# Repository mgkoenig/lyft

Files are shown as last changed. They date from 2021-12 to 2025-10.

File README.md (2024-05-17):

# LYFT
LYFT is a sophisticated remote control for the famous IKEA BEKANT desk. It replaces the original controller and adds a number of useful features for more options and convenience. 

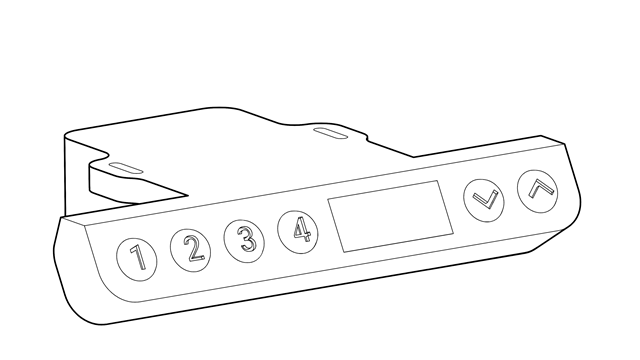
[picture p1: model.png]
lyft_model


Check [tindie](https://www.tindie.com/products/mgkoenig/lyft/) to see a fully assembled version of LYFT in action. 

If you would like to read a featured article about LYFT you can find some on [ikeahackers](https://ikeahackers.net/2024/03/ikea-adjustable-desk.html) or [hackaday](https://hackaday.com/2024/04/18/lyft-standing-up-for-better-ikea-bekant-control/) respectively. 

## Features 
#### Saving Desk Positions  
The controller can store up to four different desk positions. These positions are easily accessable using the four memory buttons.

#### Display 
The controller is equipped with a 3-digit 7-segment display which allows you to read the current desk height either in centimeters or inch. Furthermore, you can adjust the display brigtness as well as the display-on time. If the shown desk height is not accurate you can adjust the value using the 'level correction' feature by plus/minus 9 centimeters. 
  
#### Audio Signals  
In order to give some acoustic feedback the controller has a build-in audio transducer. The volume of the audio signals can be set in the settings menu but also be disabled.
  
#### Automatic Driving Mode
One of the most useful features is the automatic driving mode which allows you to move the desk to a saved position without holding a button all the time. 

#### Safety Pin 
On the basis of the original controller LYFT also supports a safety pin. The pin is needed to move the desk and to unlock the settings menu for changes. It is fully compatible with the original IKEA safety pin which is provided with the BEKANT desk. 

Further details and how to use these features are described in the [manual](/manual.pdf).

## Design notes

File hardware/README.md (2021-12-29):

# LYFT Hardware 
The LYFT hardware consists of two PCB boards. A controller board and an HMI board. 

### Controller Board
The controller board holds the SAM-D21 micrcontroller and handles all the motor control as well as the HMI communication. Desk motors are addressed using the LIN bus while the HMI board is connected via I2C. A buzzer is used to generate sounds and alarms. 

### HMI Board
The HMI board is equipped with an AS1115 display driver to control both the 7-segment display and all six buttons. 

### Library
Parts which are not existent in the standard KiCad library are published here.

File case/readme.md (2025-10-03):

# LyftV9_2 v36 (R1.00.00)

The slicer file was made for the Prusa mk3s+. 

## Print Part Combinations
### Main Body
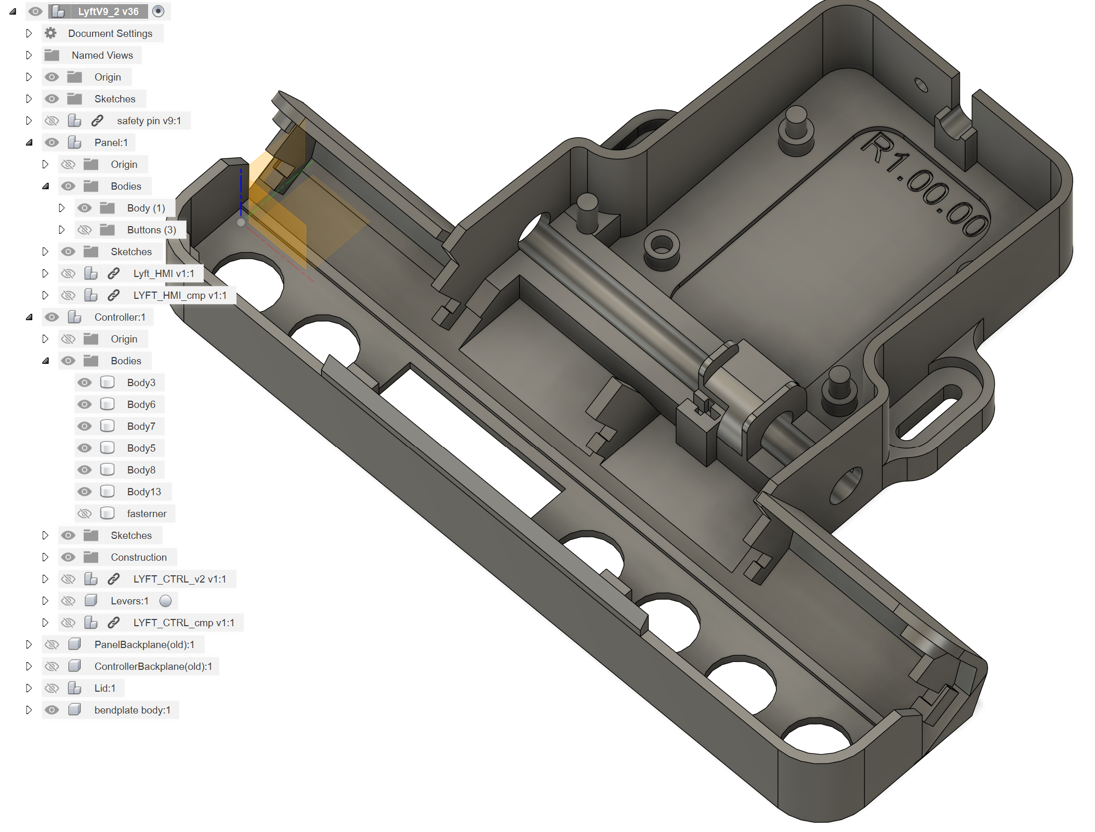
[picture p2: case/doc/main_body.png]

- Component "Panel"
  - Body Group
- Component "Controller"
  - all bodies except "fastener"
  - exclude Component "Levers"
- Component "bendplate body"

### Lid
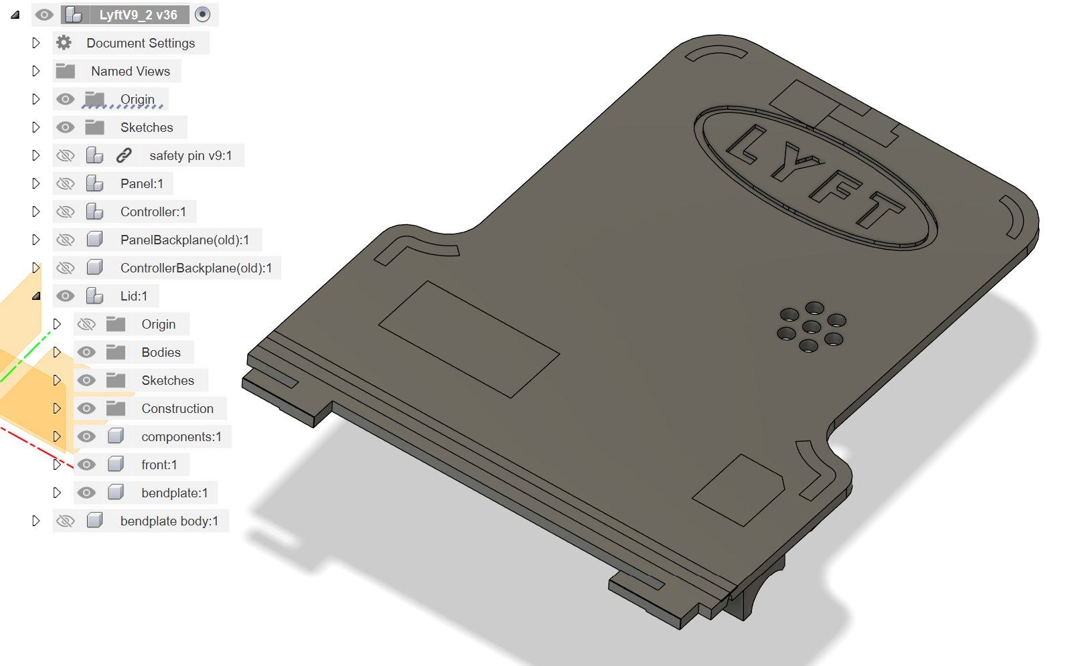
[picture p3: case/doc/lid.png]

- Component "Lid"

### Levers
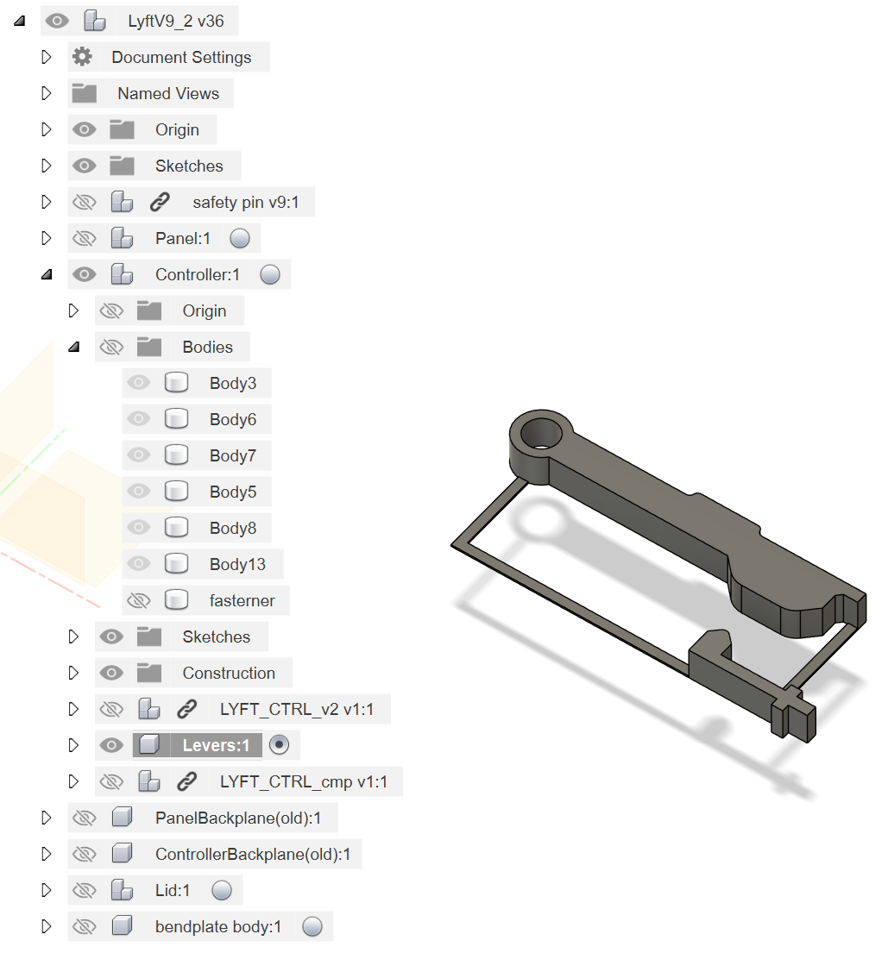
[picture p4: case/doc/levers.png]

- Component "Levers" in "Controller"
  - hide everything else

### Buttons
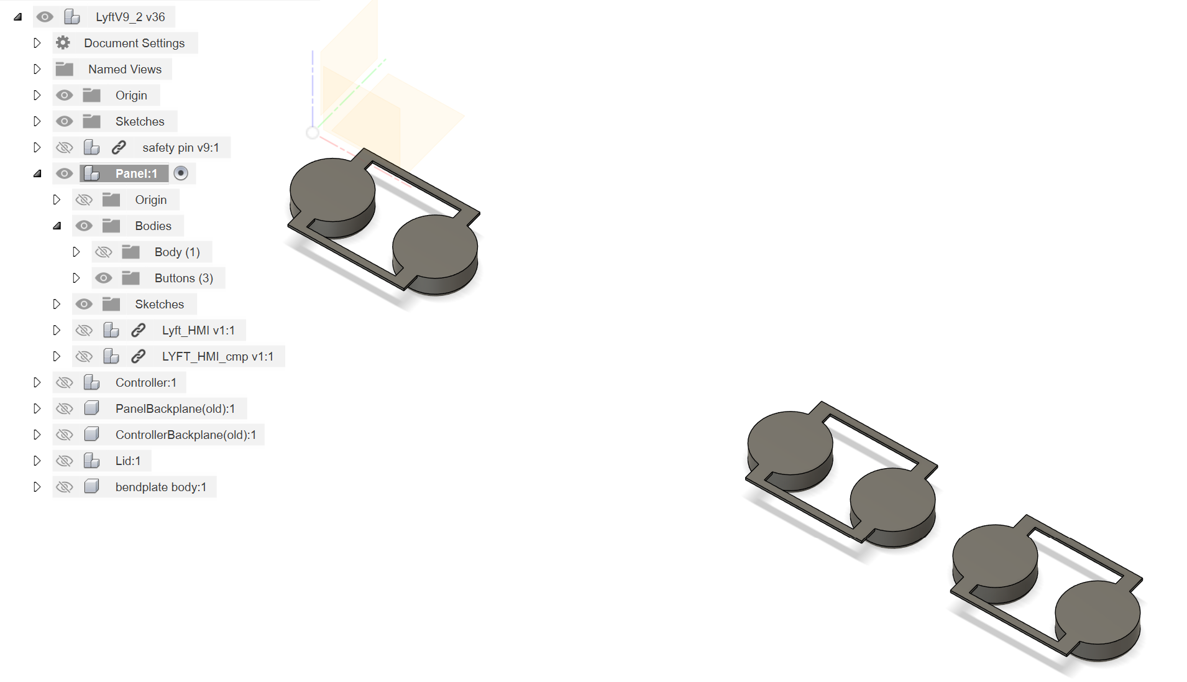
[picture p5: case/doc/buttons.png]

- Body Group "Buttons" in "Panel"
  - hide everything else

### Fasteners
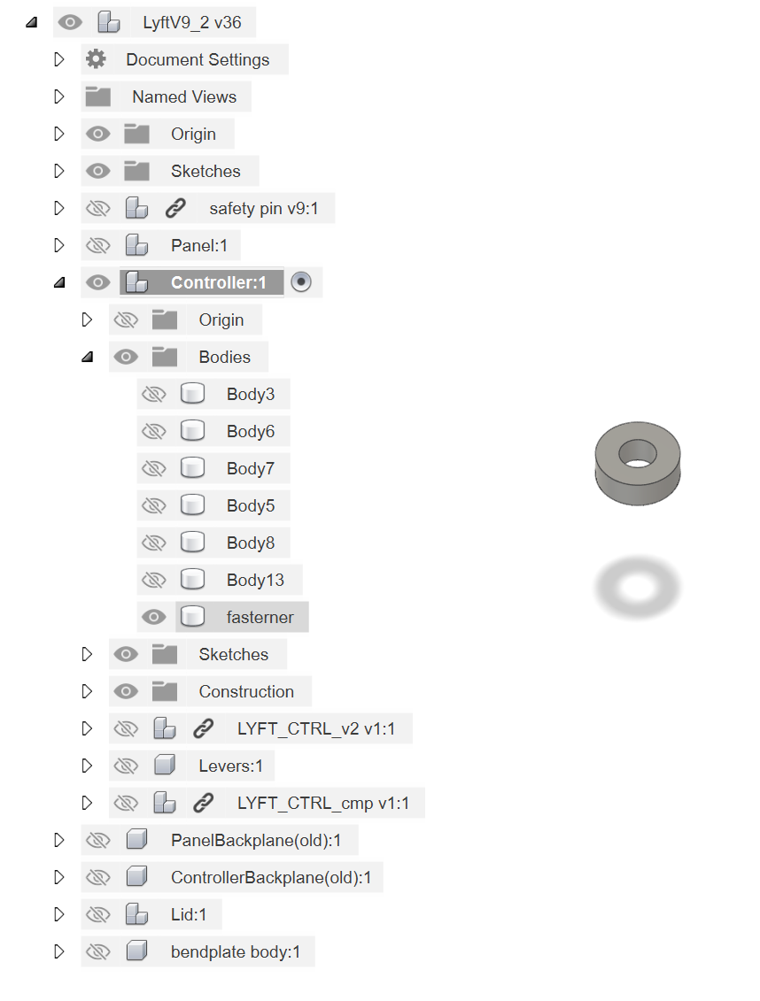
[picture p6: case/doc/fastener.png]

- Body "fastener" in "Controller"
  - hide everything else

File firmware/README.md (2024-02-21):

# LYFT Firmware
The LYFT firmware follows a classical multi-layer approach, consisting of a hardware abstraction layer (HAL), several driver modules and a simple application layer. The driver functions are separated into several files, grouped by their principal tasks. This concept allows you to port the fimrware easily to other platforms. 

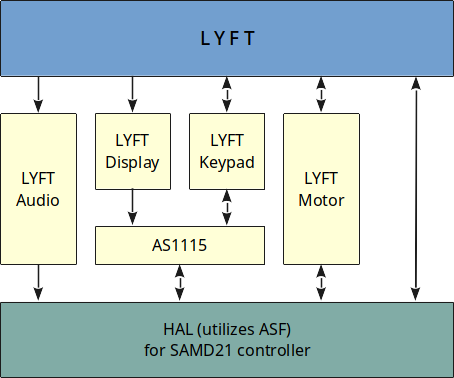
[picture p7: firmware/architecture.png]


The HAL layer utilizes the ASF framework (currently version 3.49.1) for Microchip's SAM MCU's with the following components:
- DAC (callback) [for audio volume control]
- EXTINT (callback) [get notified of keypad inputs]
- NVM [saving configuration and desk positions]
- PORT [GPIO pin control]
- SERCOM I2C (callback) [talk to AS1115 LED controller]
- SERCOM USART (polled) [using a UART module for LIN communication]
- SYSTEM (core system drivers)
- TC (callback) [handling motor timings, keypad timings ond more]
- TCC (callback)

The LYFT drivers are separated into four modules: 
- Audio: all functins related to audio features
- Display: all functions related to the display
- Keypad: all functins to evaluate keystrokes and holding times
- Motor: all functions to control the motors including LIN bus communication

For the AS1115 display driver IC a discrete driver unit was written.

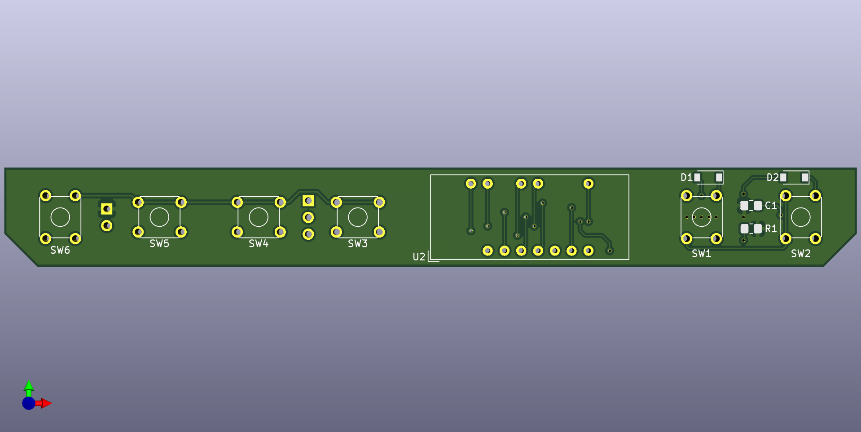
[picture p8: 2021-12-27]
hardware/HMI Board/Rev A/doc/pcb_front.png

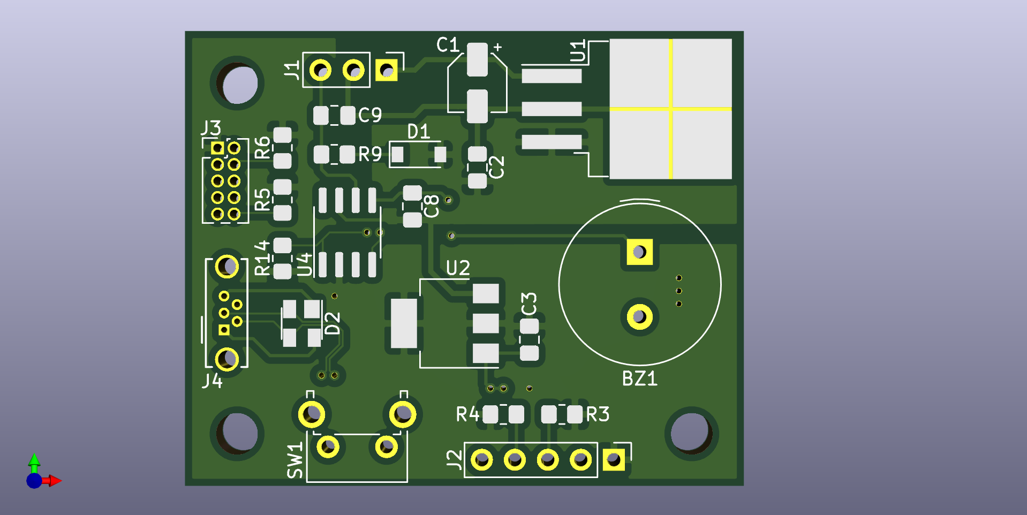
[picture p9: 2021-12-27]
hardware/Controller Board/Rev A/doc/pcb_front.png

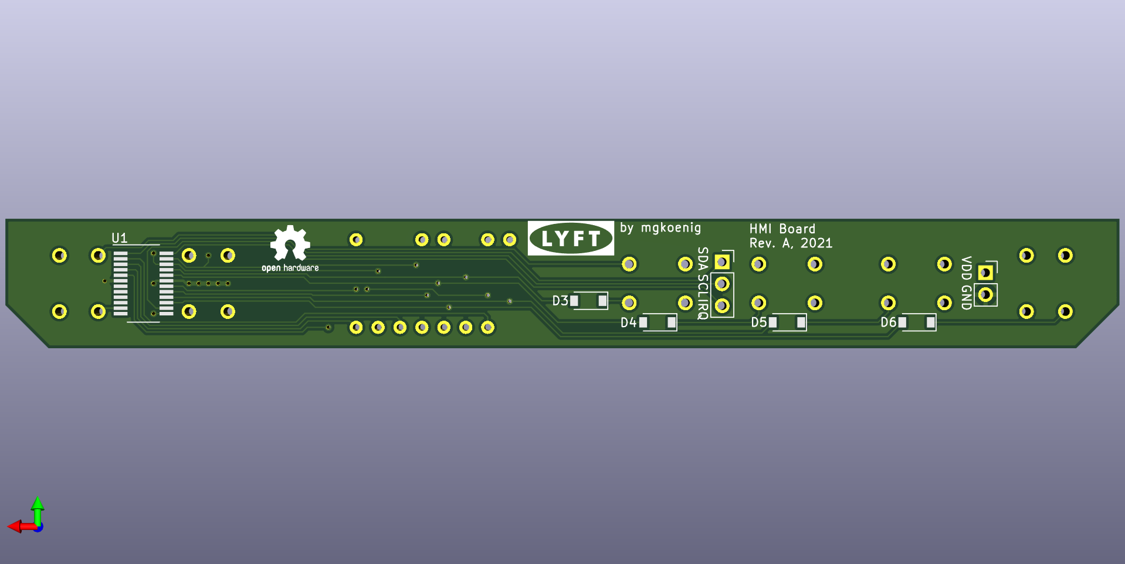
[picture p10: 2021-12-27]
hardware/HMI Board/Rev A/doc/pcb_back.png

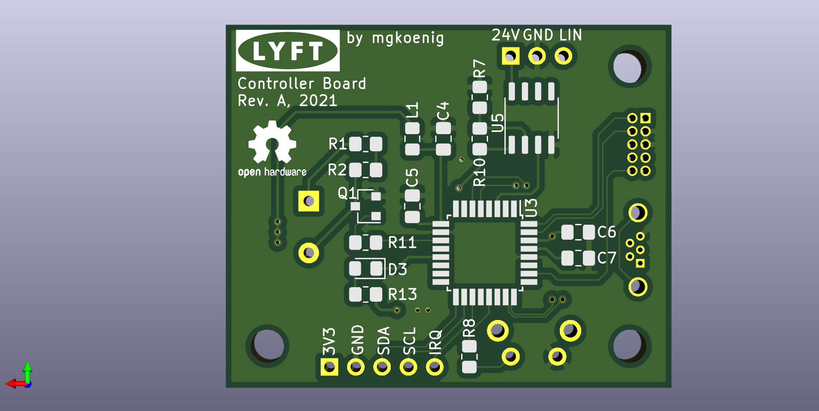
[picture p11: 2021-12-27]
hardware/Controller Board/Rev A/doc/pcb_back.png

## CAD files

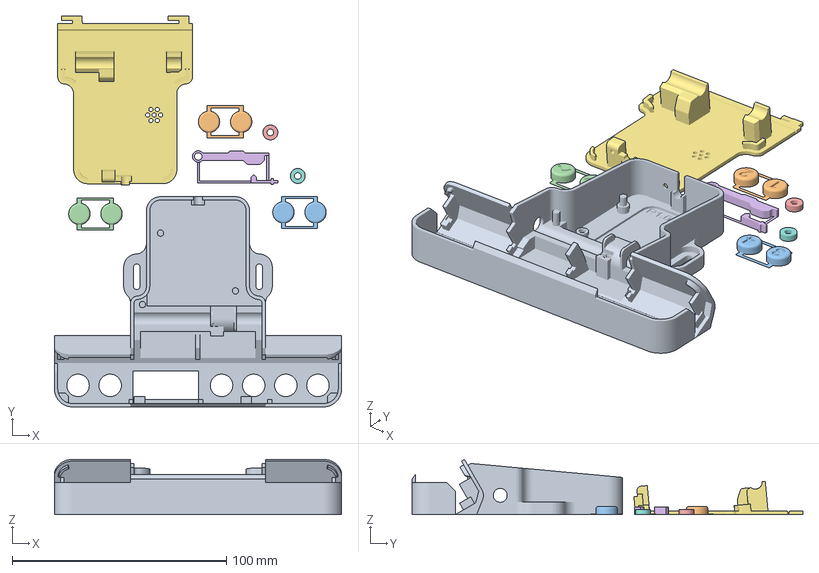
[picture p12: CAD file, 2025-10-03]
case/Lyft_caseR1.3mf
134.2 x 182.5 x 25.8 mm
LyftV9_2 v35 controller R1.00.00.stl
LyftV9_2 v35 buttons_12.stl
LyftV9_2 v35 buttons_34.stl
LyftV9_2 v35 buttons_ud.stl
LyftV9_2 v35 fastener.stl x 2
LyftV9_2 v35 levers.stl
LyftV9_2 v35 Lid R1.00.00.stl

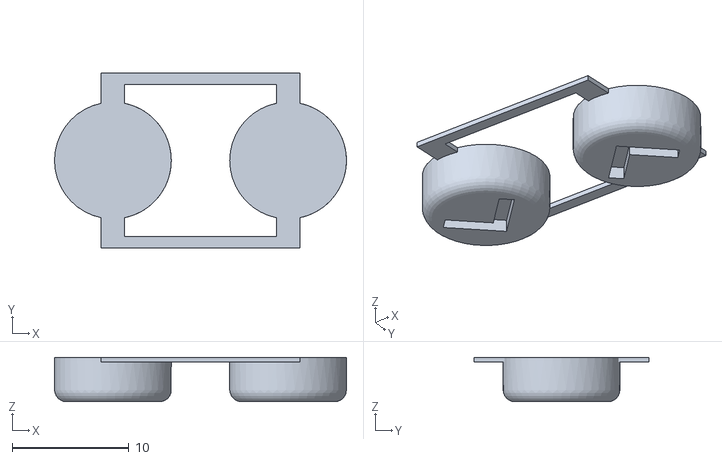
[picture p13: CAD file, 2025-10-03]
case/Lyft_caseR1_buttons_ud.stl
25.0 x 15.0 x 3.80

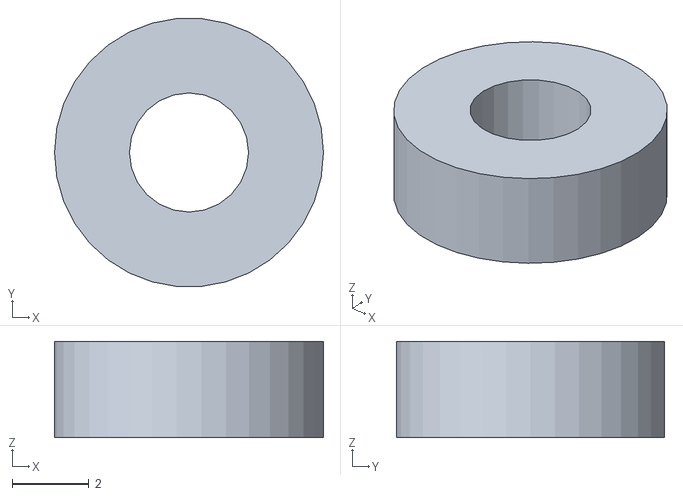
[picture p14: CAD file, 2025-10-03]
case/Lyft_caseR1_fastener.stl
7.00 x 6.97 x 2.50

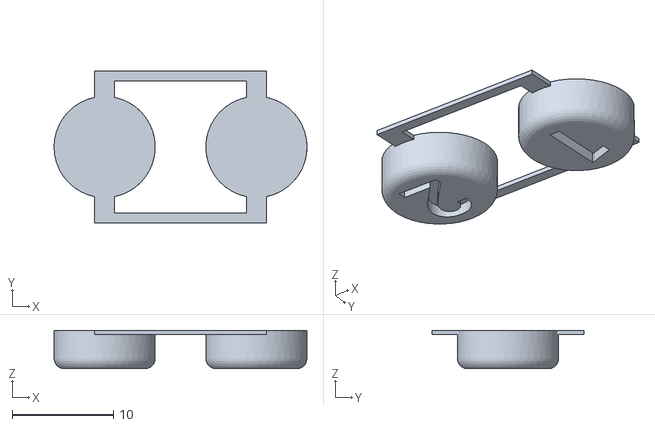
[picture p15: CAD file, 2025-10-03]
case/Lyft_caseR1_buttons_12.stl
25.0 x 15.0 x 3.80

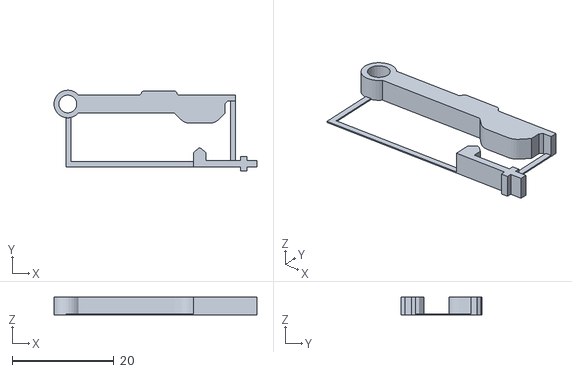
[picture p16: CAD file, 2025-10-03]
case/Lyft_caseR1_levers.stl
39.9 x 15.8 x 3.50

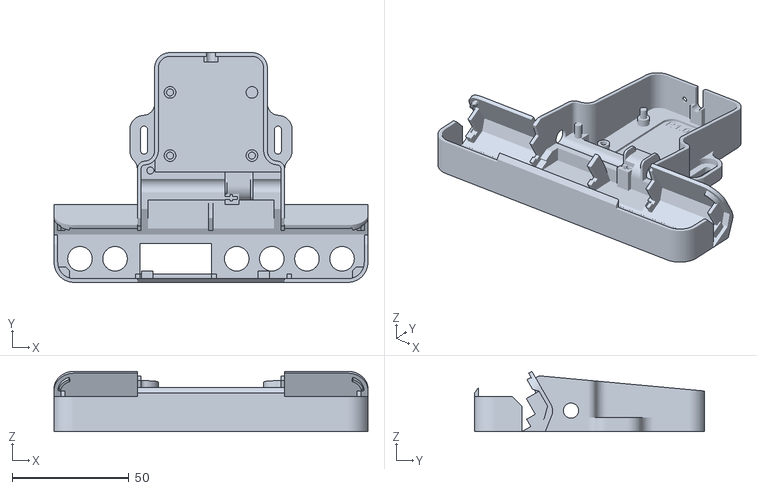
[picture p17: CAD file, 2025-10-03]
case/Lyft_caseR1_controller.stl
134.2 x 98.2 x 25.8

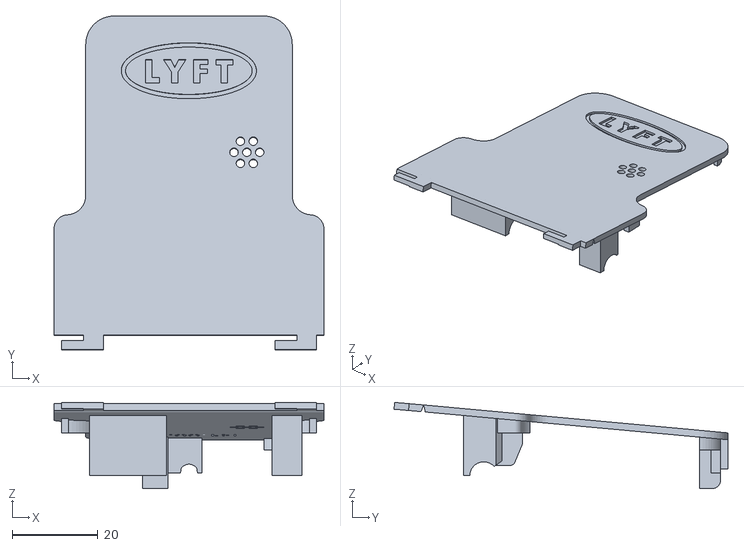
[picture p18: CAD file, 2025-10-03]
case/Lyft_caseR1_lid.stl
63.0 x 77.9 x 20.1

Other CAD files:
case/Lyft_caseR1_buttons_34.stl

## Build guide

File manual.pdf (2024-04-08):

# LYFT


### I M P O R TA N T I N F O R M AT I O N

LYFT is a sophisticated remote control for electric height adjustable desks, compatible with

the famous IKEA BEKANT desk. Designed as a plug & play solution, you can easily replace

your originally provided remote control. LYFT comes completely assembled and is ready to

use out of the box.

This project is an open-source DIY project and comes therefore without any liability or

warranty. Usage of LYFT is always at your own risk. The originator is not liable of any

damage | the | remote | might | cause. | All | source | files | are | published | on | GitHub

(github.com/mgkoenig/lyft) and licenced under the GPL-3.0 license. Feel free to take a closer

look at the design or to improve LYFT with even more useful features customized to your

needs.

All product and company names are trademarks™ or registered® trademarks of their

respective holders. Use of them does not imply any affiliation with or endorsement by

them. IKEA is a registered trademark of Inter IKEA Systems BV.

Disclaimer of liability: In no event shall the originator be liable for any direct, indirect,

punitive, incidental, special, consequential damages, to property or life, whatsoever

arising out of or connected with the use or misuse of this product.

Exclusions from warranties: By purchasing this product you expressly agree that use of this

product is at your sole risk. The originator does not and cannot warrant that the product

will operate without errors.

All information and products described in this manual are provided on an “AS IS” basis.

The originator does not make any representations or warranties of any kind, express or

implied as to the operation of this product or the information made available to you,

including implied warranties of merchantability and fitness for a particular purpose.

Furthermore, the originator's warranties for this product exclude any claims by the

customer based on defects in the product caused by the customer, or by third parties

beyond the originator's control.

2 | Document version 1.0 (02/2024)

### F U N C T I O N A L L AY O U T

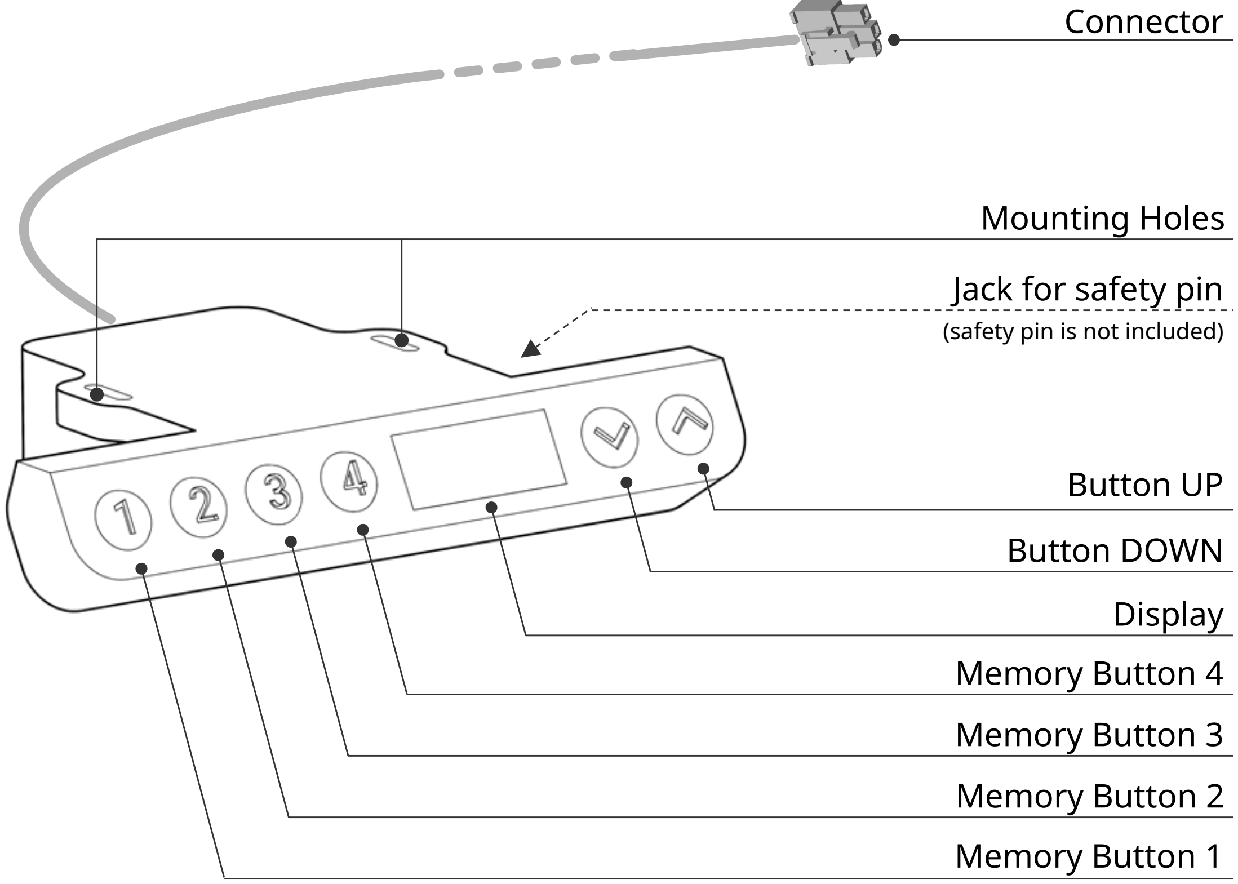
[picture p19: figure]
Connector; Button UP; Button DOWN; Display; Memory Button 4; Memory Button 3; Memory Button 2; Memory Button 1; Jack for safety pin; Mounting Holes; (safety pin is not included)

### I N S TA L L AT I O N

In order to use LYFT, choose your preferred handling side and mount the remote control

on the bottom edge of the desk. Use the destined mounting holes on the housing. Since

no screws are provided with the shipment, you might use the original screws which were

delivered together with the desk or use any two conventional [3 x 16mm] or [4 x 5/8”]

wood screws instead.

Finally plug the cable into its designated connector on the motor box. You can find the

motor box on top of each leg (beneath the table top). If you’re uncertain how to connect

the cable, refer to the original IKEA BEKANT assembly instructions.

Compatible with firmware version 1.1.0. | 3

### B A S I C F E AT U R E S

S A F E T Y P I N

LYFT is equipped with a safety mechanism to prevent unintended desk movements.

Therefore, a safety pin must be plugged in whenever you want to change the desk height

or configuration settings. The safety pin is not provided with the LYFT remote control, but

fully compatible with the safety pin that comes with your IKEA BEKANT desk. If you have

lost your pin, you can easily (and mostly for free) order it as a spare part from your local

IKEA store. Please find the correct part number in the original assembly instructions. If no

safety pin is connected, all features are locked and the display shows the following screen:

M O V I N G U P

To move your desk upwards, just press and hold the UP button on your LYFT remote

control. The motors will automatically stop as soon as you release the button or the upper

limit of the height is reached.

M O V I N G D O W N

To move your desk downwards, just press and hold the DOWN button on your LYFT

remote control. The motors will automatically stop as soon as you release the button or

the lower limit of the height is reached.

M O V I N G T O A S A V E D P O S I T I O N

If you have previously saved a comfortable desk position to one of the memory buttons

(see the description in the upcoming settings chapter), you can move the desk to this

height by pressing and holding the corresponding button. In case no position was saved

so far, the display shows the following screen:

### S E T T I N G S M E N U

E N T E R T H E S E T T I N G S M E N U

In order to make any changes of the settings or to save a current desk position, you need

to enter the settings menu. The menu is accessed by pressing the UP and DOWN buttons

simultaneously for at least 2 seconds.

N A V I G A T E T H E S E T T I N G S M E N U

You can walk through the settings menu by using the UP and DOWN buttons to scroll to

the next or previous page respectively.

L E A V E T H E S E T T I N G S M E N U

To exit the settings menu nothing special has to be done. Six seconds after the last button

was pressed, the menu will save all its current settings and return to its default screen,

showing the desk height.

Compatible with firmware version 1.1.0. | 5

2 sec.

S A V E A P O S I T I O N [ P ]

To save the current desk position, just enter the settings menu. The first entry of the menu

shows a [P] which stands for position. By pushing one of the four memory buttons you will

save the current height to the selected button.

D I S P L A Y B R I G H T N E S S [ L ]

You can change the brightness of the display to four different levels. Navigate within the

settings menu to page [L]. Then, select the intensity by pushing one of the four memory

buttons. Each button sets the brightness to a pre-defined value.

A U D I O C O N T R O L [ A ]

LYFT is equipped with a built-in audio transducer to generate audio signals and alarms.

You can set the volume of these signals or turn them off completely. Navigate to menu

page [A] and set your preferred loudness pushing one of the four memory buttons. Button

1 will turn this feature off while the others set a certain volume level. A beep tone will

demonstarte the selected volume after each keystroke.

D I S P L A Y - O N T I M E [ F ]

After pushing a button or adjusting the desk height to your preferred position, the display

will stay on for a couple of seconds. You can change the display-on time on menu page [F].

Choose between 5, 10, 15 or 20 seconds display-on time using the memory buttons.

M E A S U R E M E N T U N I T [ U ]

By default the height of the desk is shown in centimeters. However, you can change the

dispayed unit to inch. Go to the unit page [U] within the menu and select your preferred

measurement unit using memory button 1 or 2.

D E S K M O V I N G M O D E [ G ]

LYFT supports two driving modes to move the desk to saved position – either manually

(‘hand-driven’) or automatically. When Hand-driven mode is selected, you need to press

and hold the designated memory button until its final desk height is reached. If Automatic

mode is selected, you just need to press the memory button for 1.5 seconds, then the

desk moves by itself to the final position without further interaction. An automatically

moving desk can be stopped by pushing any button on the remote control. Use memory

buttons 1 or 2 to select your preffered moving mode.

Please note: manual mode is safer while automatic mode is more comfartable.

L E V E L C O R R E C T I O N [ C ]

The shown desk height might not be accurate due to level adjustment screws or a thicker

tabletop. Therefore, you have the opportunity to tune the displayed position. Go to the

level correction page [C] and set an offset value to the current height. The offset range is

between plus/minus 9 centimeters. The offset value is always set as centimeter value – no

matter which measurement unit you have selected. Use memory buttons 1 or 2 to

increase or decrease the value.

Compatible with firmware version 1.1.0. | 7

D R I F T I N F O R M A T I O N [ d ]

This menu page is just an informational entry. The drift value tells you the absolute

variation of both motor positions to each other (the smaller the value the better). However,

please keep in mind, this value does not represent centimeters or inches – it’s related to

an internal counting value.

### T R O U B L E S H O O T I N G

In rare cases, it might happen that the motors don’t respond to entries of the LYFT remote.

This error is related to a failed initialization process during the start up phase, when the

remote was connected to the motor box.

In such a case, please disconnect your IKEA BEKANT desk from the power outlet for five

minutes and try again. You can still double-check the flawless operation of your desk using

the original remote control.

### A C K N O W L E D G M E N T S

Many thanks to Marian for his generosity and support! He enriched this project

continuously with great ideas, designed and produced a fabulous housing for the LYFT

remote control.

Thanks to Greg Cormier and his megadesk project (github.com/gcormier/megadesk) for

sharing his findings about the IKEA BEKANT functionality and bus communication.

All icons by icons8.com.

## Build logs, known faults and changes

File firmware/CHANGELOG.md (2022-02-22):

# Changelog

## Version 1.0.0 (22 Feb 2021)
Initial commit. This version runs stable on the provided hardware (both boards Rev A) and includes the following features and drivers: 
- Desk moving up/down
- Four memory positions
- Display shows current desk height as cm or inch value (unit control)
- Display brightness control
- Audio feedback (with volume control)
- Level correction (to adjust the shown desk height)
- Tells the drift of both motors
- Support of the safety pin

User settings (like display brightness, volume control, desk positions) can be stored permanently to the NVM.

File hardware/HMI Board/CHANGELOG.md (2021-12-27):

# Changelog
All notable changes to this project will be documented in this file.
## Revision A (Dec. 2021)
### Features:
- 130x15mm board size
- AS1115 display driver to control 7-segment display and read button states
- 3-digit 7-segment display
- 6 tactile switches

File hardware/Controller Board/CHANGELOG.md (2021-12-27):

# Changelog

All notable changes to this project will be documented in this file.

## Rev. A (Dec. 2021)
### Features
- 43x35mm board size
- SAM-D21 controller
- Buzzer for audio signals
- USB interface placed but unused

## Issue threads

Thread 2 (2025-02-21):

Add case design

black9404, 2025-02-21:
Could you please add the STL files for the case? Would be nice to be able 3D print it to make changes and possible improvements

mgkoenig, 2025-10-03:
Sorry for the delay. The STL files of the case are now available.

Closed 2025-10-03.

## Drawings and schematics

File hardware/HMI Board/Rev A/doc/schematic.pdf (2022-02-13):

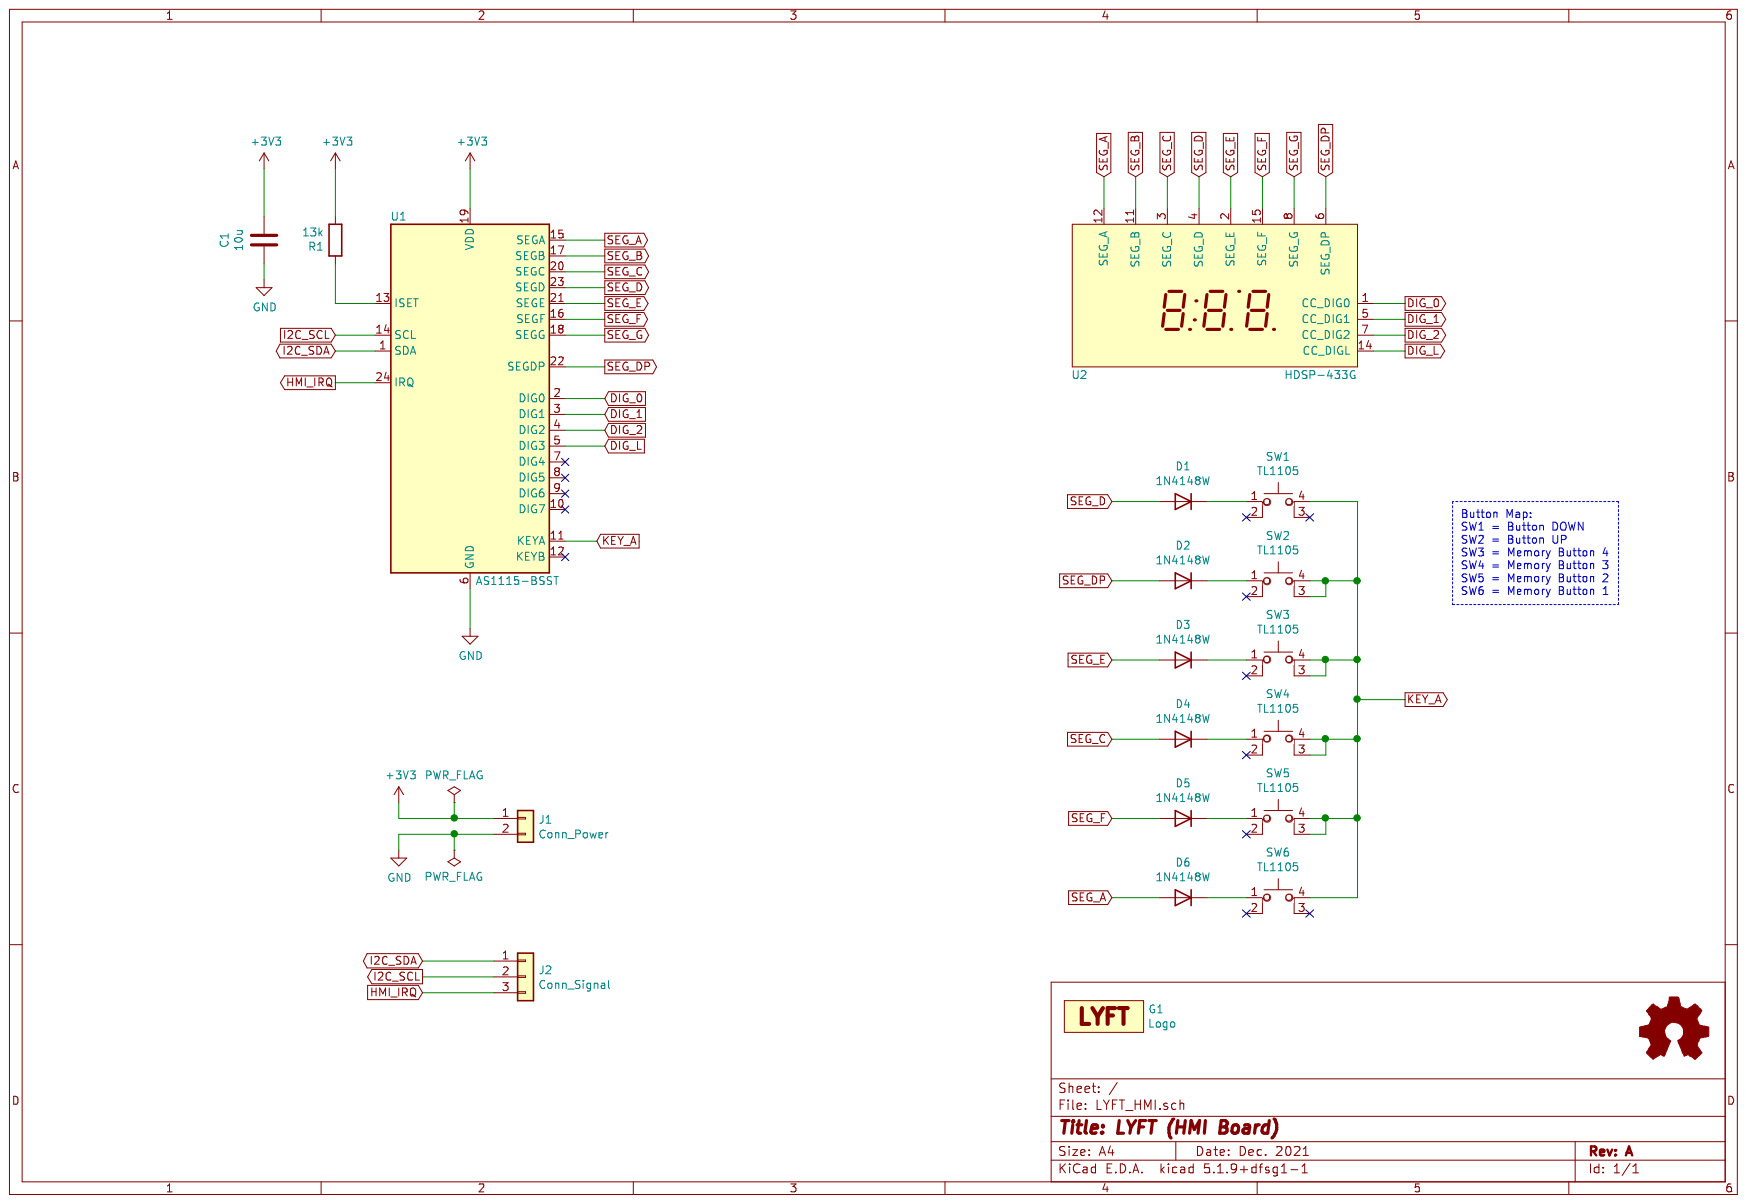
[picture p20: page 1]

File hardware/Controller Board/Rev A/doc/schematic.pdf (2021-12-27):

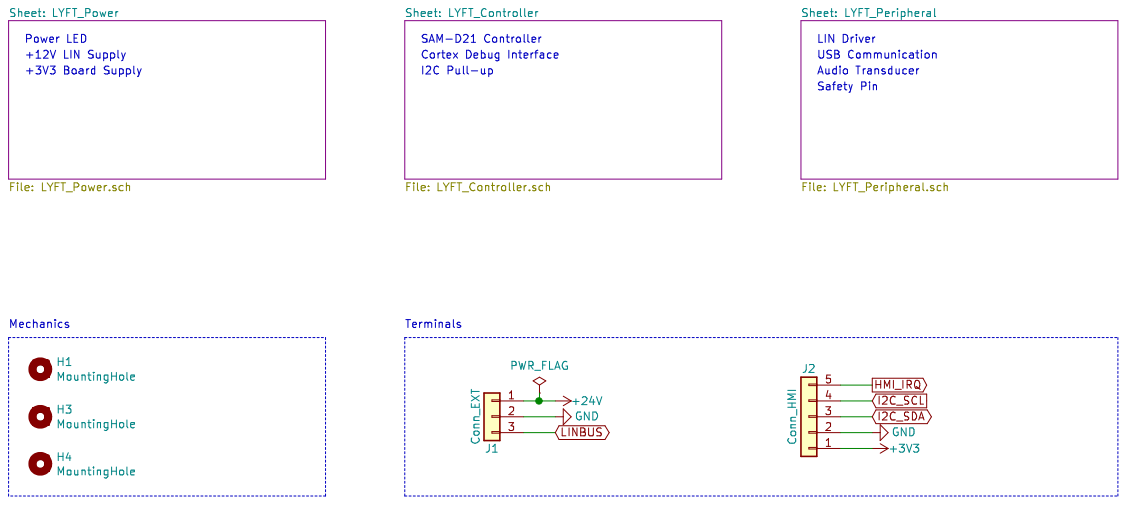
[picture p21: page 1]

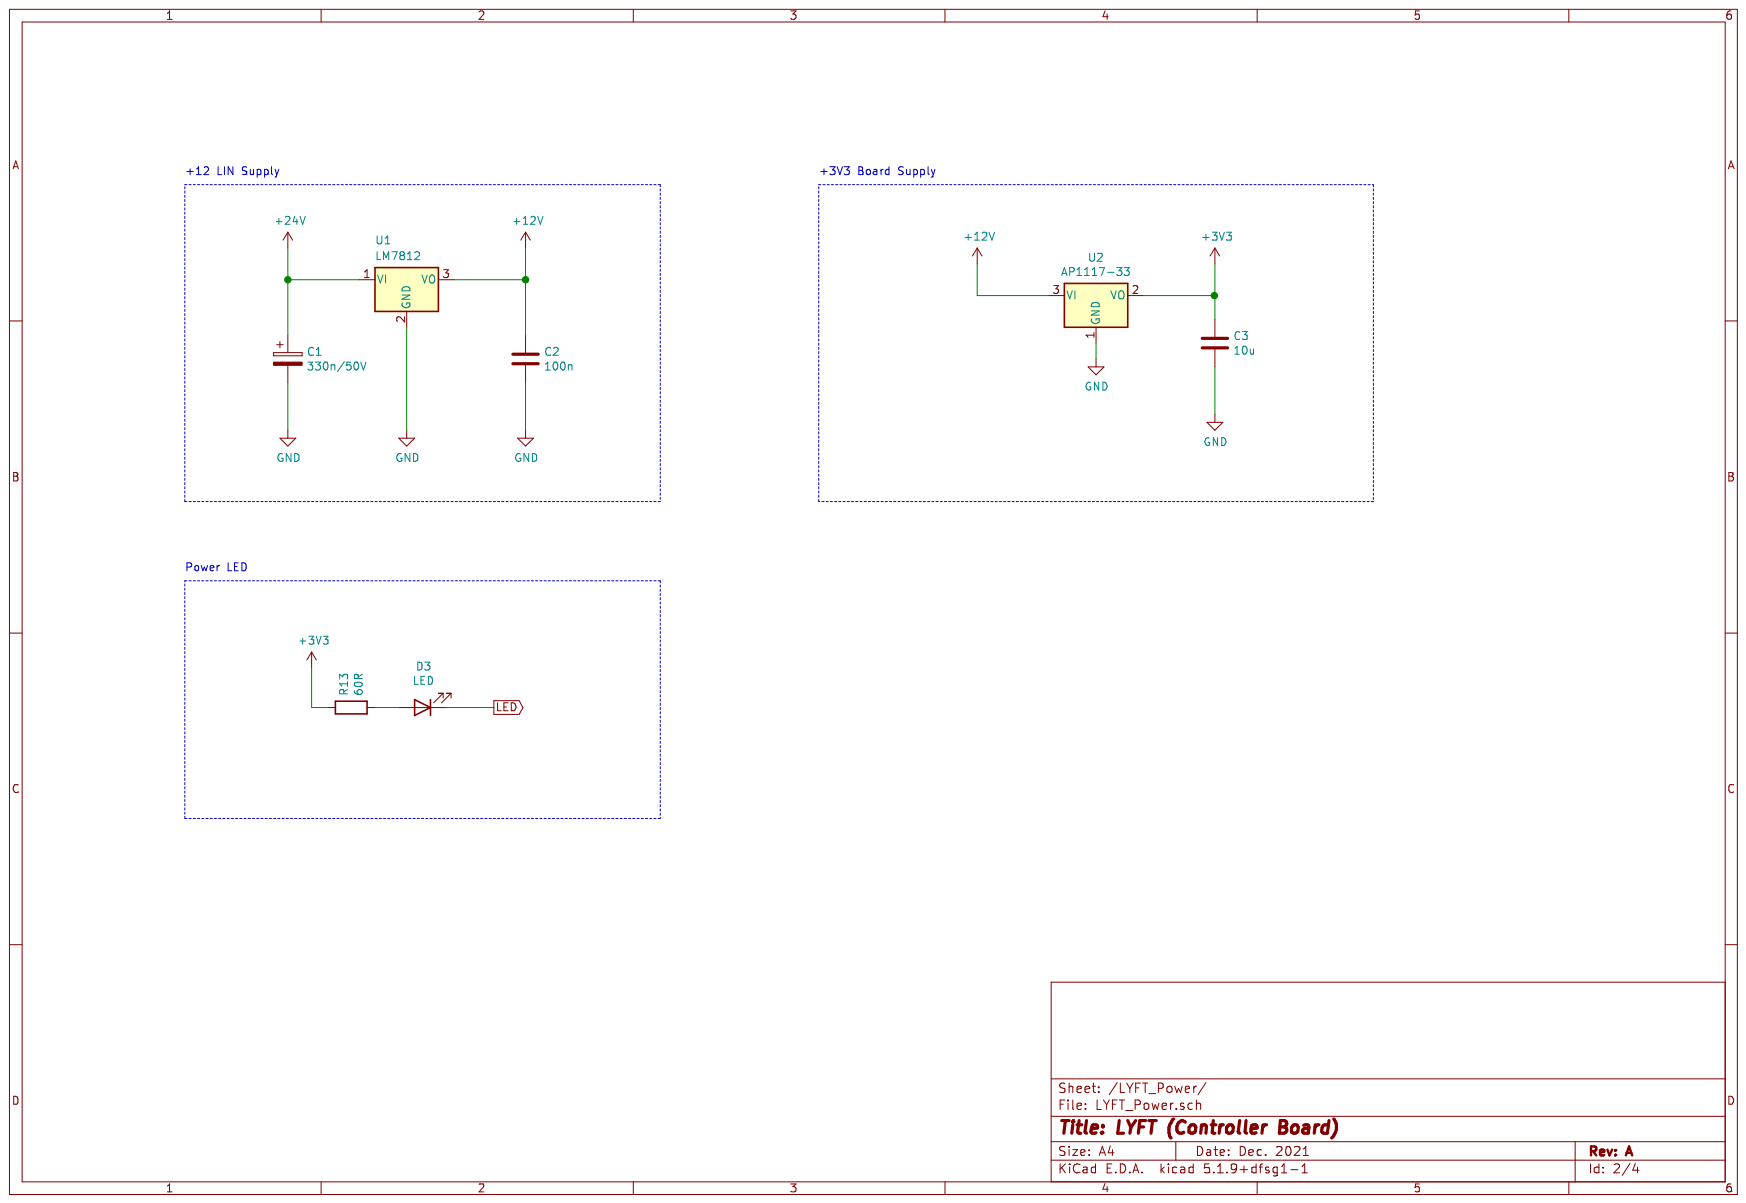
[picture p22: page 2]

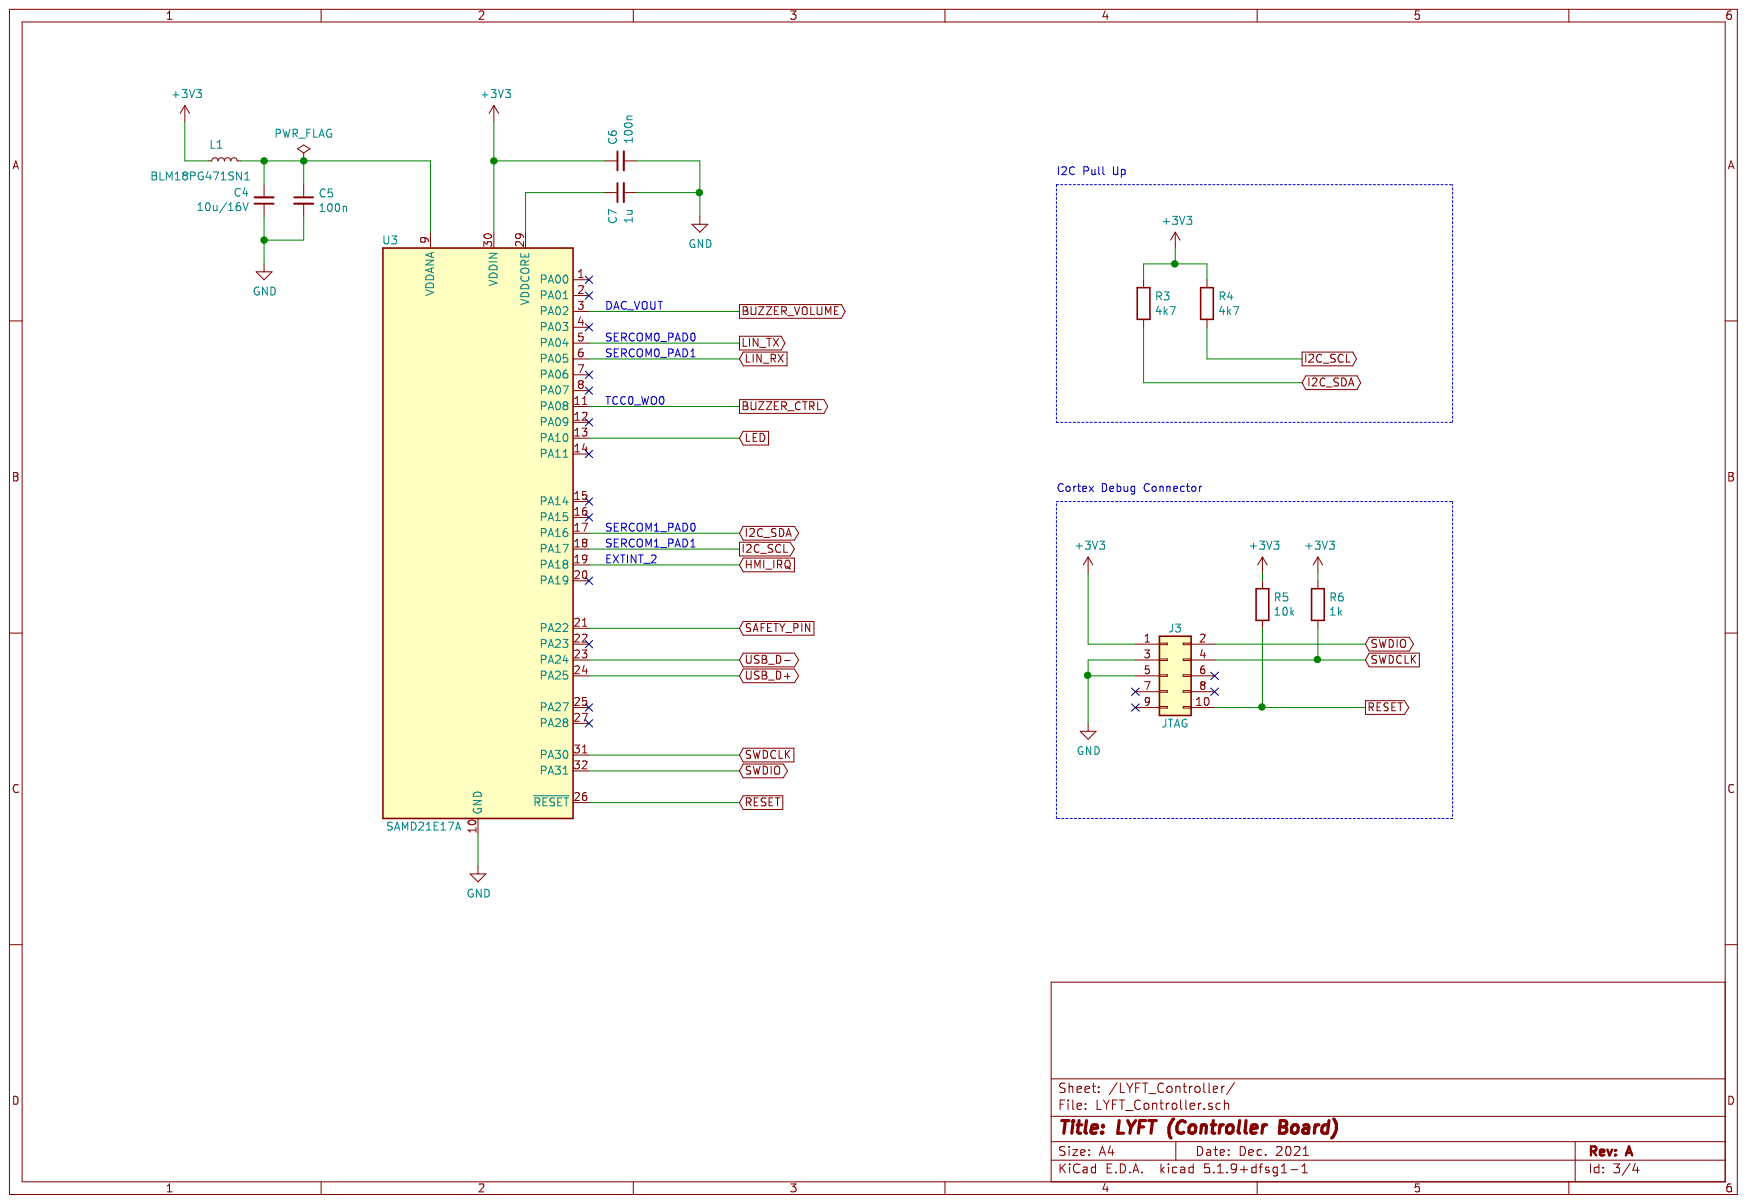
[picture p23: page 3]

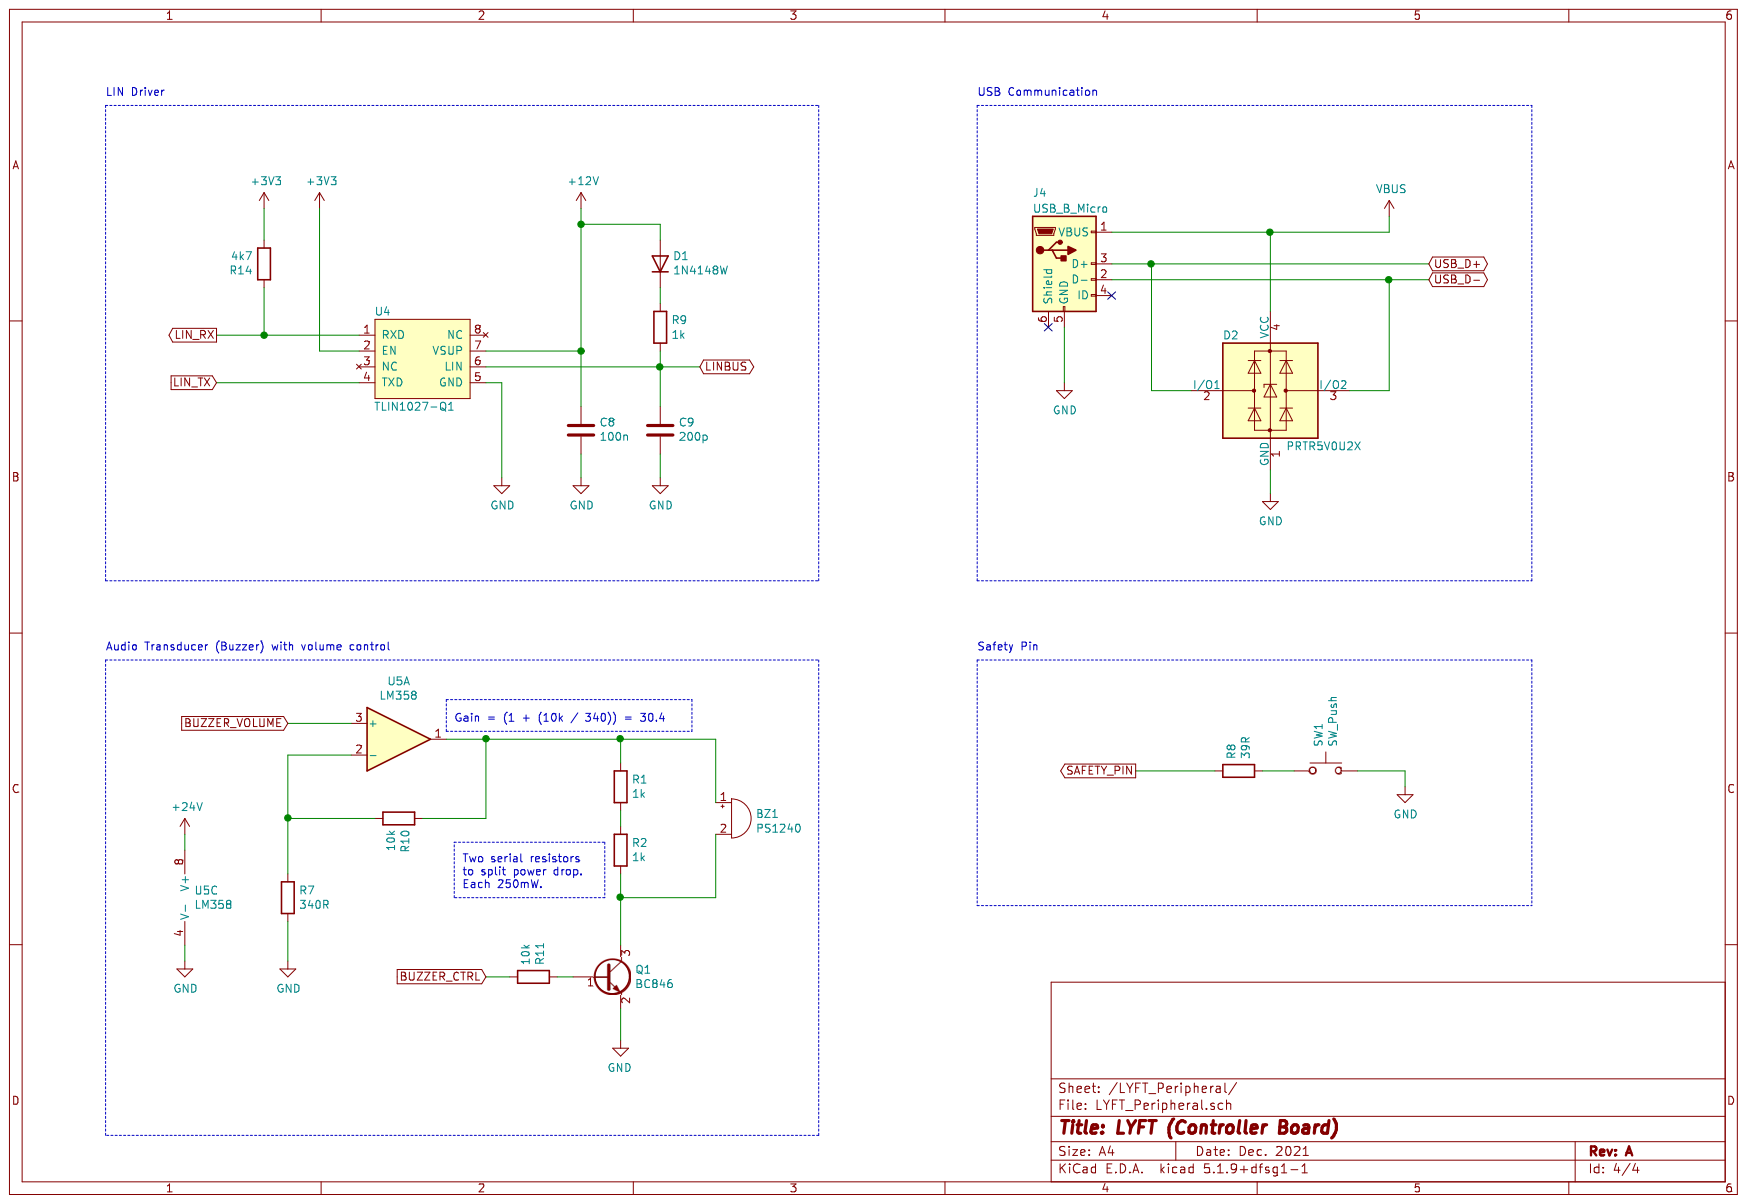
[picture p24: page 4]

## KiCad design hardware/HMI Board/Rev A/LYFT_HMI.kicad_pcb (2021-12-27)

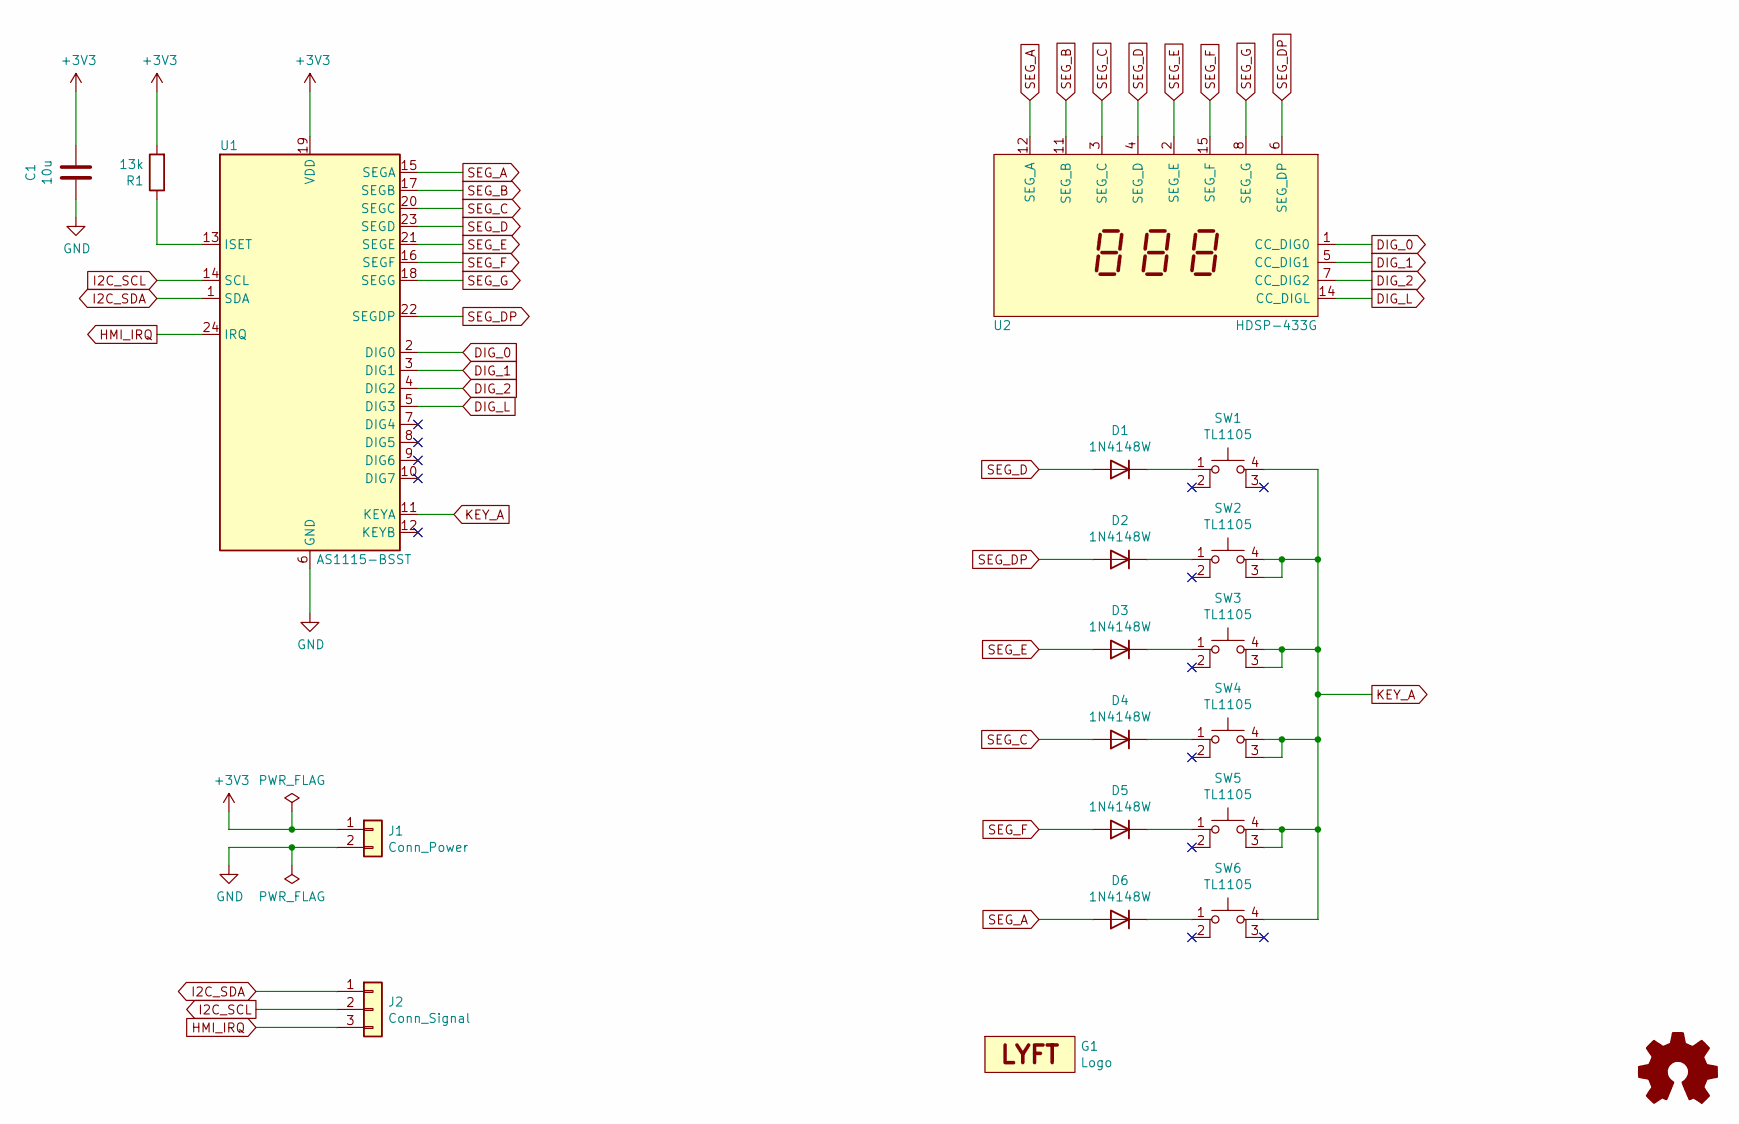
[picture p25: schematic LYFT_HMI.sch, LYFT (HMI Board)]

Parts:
C1: 10u; C_0805_2012Metric_Pad1.18x1.45mm_HandSolder
D1, D2, D3, D4, D5, D6: 1N4148W; D_SOD-123
G1: Logo; LYFT-Logo_10x4
J1: Conn_Power; PinSocket_1x02_P2.54mm_Vertical
J2: Conn_Signal; PinSocket_1x03_P2.54mm_Vertical
R1: 13k; R_0805_2012Metric_Pad1.20x1.40mm_HandSolder
SW1, SW2, SW3, SW4, SW5, SW6: TL1105; SW_TH_Tactile_Omron_B3F-10xx_Center
U1: AS1115-BSST; QSOP-24_3.9x8.7mm_P0.635mm
U2: HDSP-433G; HDSP-433

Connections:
+3V3: C1.1, J1.1, R1.2, U1.19 (VDD)
DIG_0: U1.2 (DIG0), U2.1 (CC_DIG0)
DIG_1: U1.3 (DIG1), U2.5 (CC_DIG1)
DIG_2: U1.4 (DIG2), U2.7 (CC_DIG2)
DIG_L: U1.5 (DIG3), U2.14 (CC_DIGL)
GND: C1.2, J1.2, U1.6 (GND)
HMI_IRQ: J2.3, U1.24 (IRQ)
I2C_SCL: J2.2, U1.14 (SCL)
I2C_SDA: J2.1, U1.1 (SDA)
KEY_A: SW1.4 (A), SW2.3 (K), SW2.4 (A), SW3.3 (K), SW3.4 (A), SW4.3 (K), SW4.4 (A), SW5.3 (K), SW5.4 (A), SW6.4 (A), U1.11 (KEYA)
unnamed: D1.1 (K), SW1.1
unnamed: D2.1 (K), SW2.1
unnamed: D3.1 (K), SW3.1
unnamed: D4.1 (K), SW4.1
unnamed: D5.1 (K), SW5.1
unnamed: D6.1 (K), SW6.1
unnamed: R1.1, U1.13 (ISET)
SEG_A: D6.2 (A), U1.15 (SEGA), U2.12 (SEG_A)
SEG_B: U1.17 (SEGB), U2.11 (SEG_B)
SEG_C: D4.2 (A), U1.20 (SEGC), U2.3 (SEG_C)
SEG_D: D1.2 (A), U1.23 (SEGD), U2.4 (SEG_D)
SEG_DP: D2.2 (A), U1.22 (SEGDP), U2.6 (SEG_DP)
SEG_E: D3.2 (A), U1.21 (SEGE), U2.2 (SEG_E)
SEG_F: D5.2 (A), U1.16 (SEGF), U2.15 (SEG_F)
SEG_G: U1.18 (SEGG), U2.8 (SEG_G)

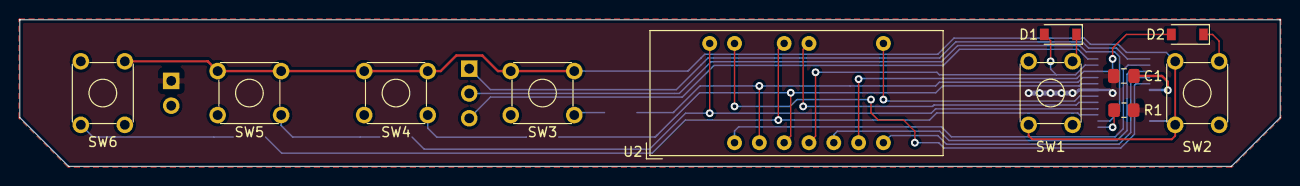
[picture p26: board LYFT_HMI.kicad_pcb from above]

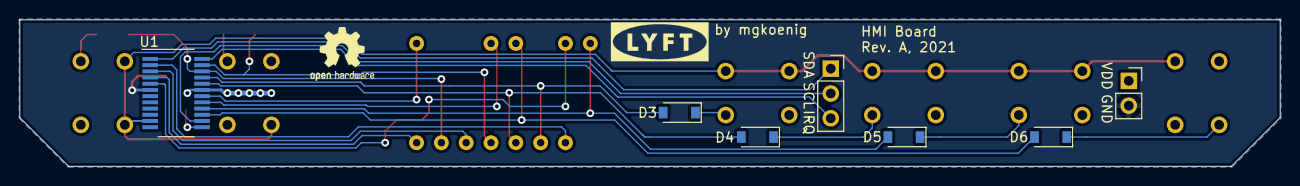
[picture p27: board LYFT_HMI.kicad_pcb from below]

Board: 2 copper layers, 129.0 x 15.0 mm, 19 parts (8 on the bottom side), 25 nets.

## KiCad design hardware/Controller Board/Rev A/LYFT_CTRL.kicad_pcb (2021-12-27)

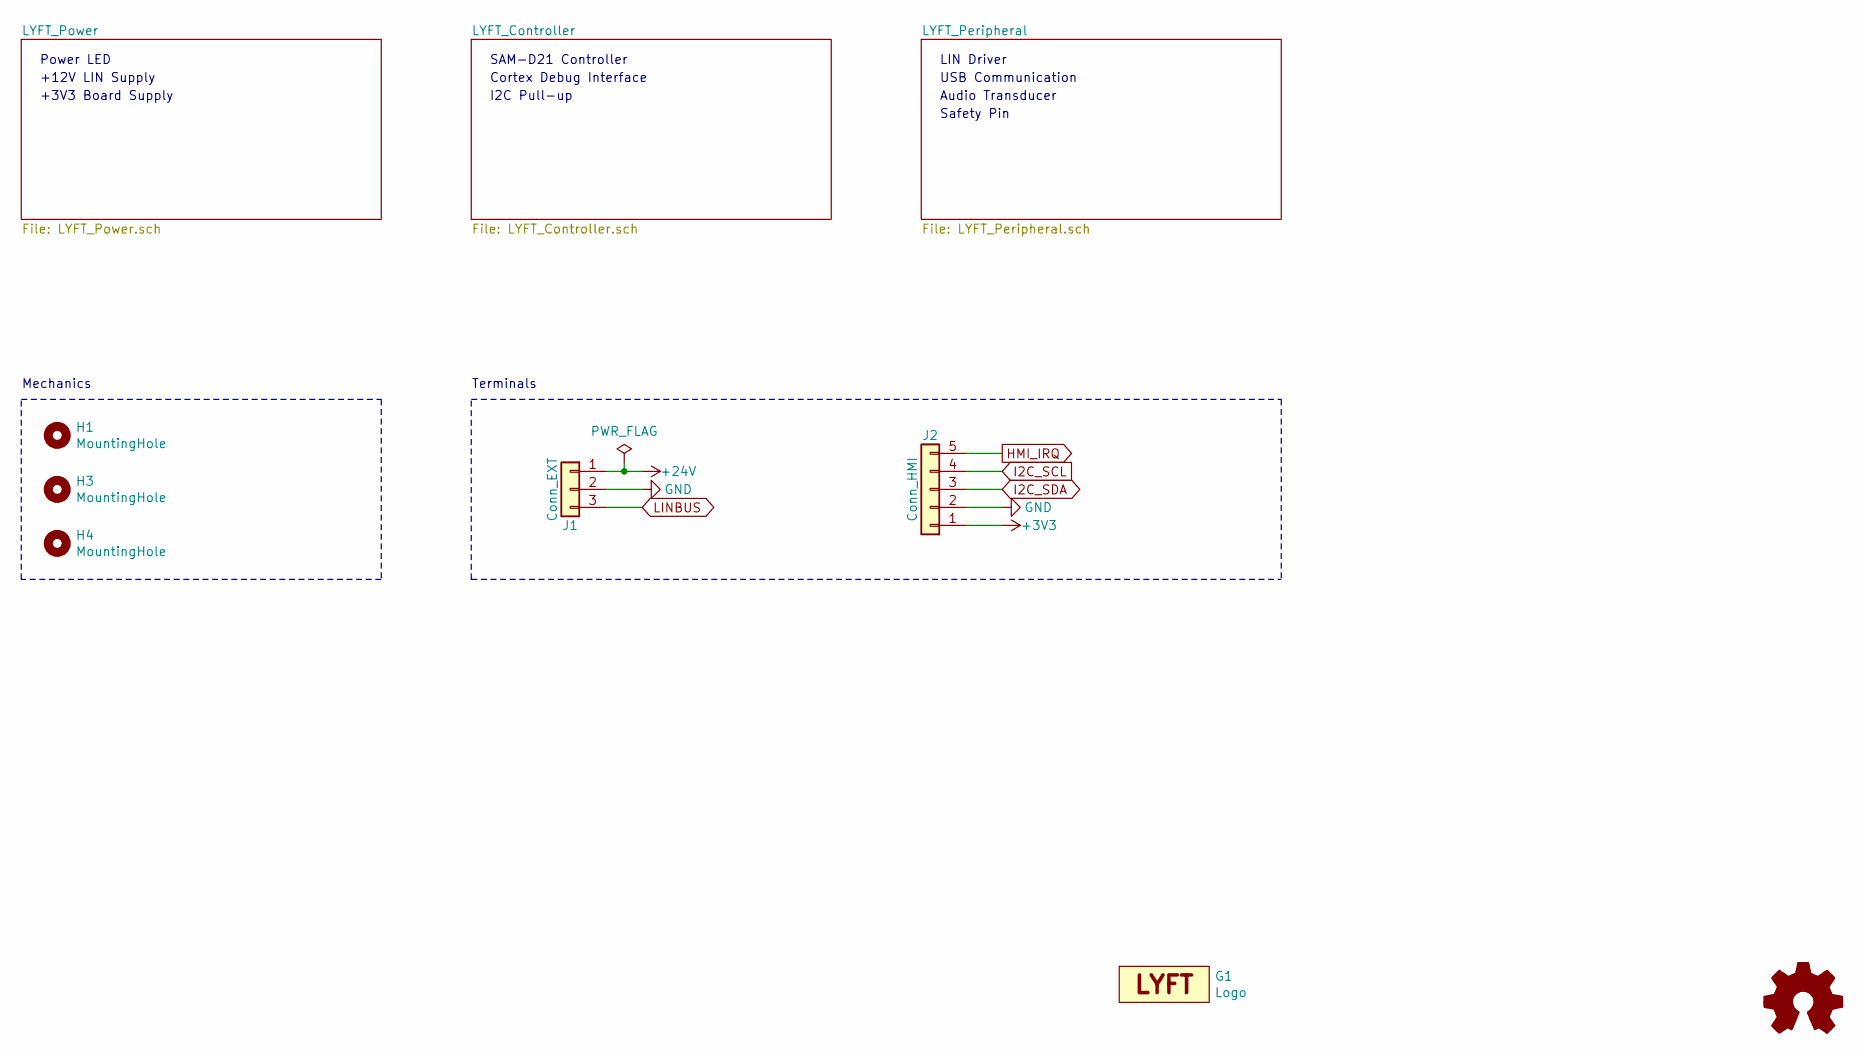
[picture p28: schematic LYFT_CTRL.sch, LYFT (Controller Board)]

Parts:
G1: Logo; LYFT-Logo_10x4
H1, H3, H4: MountingHole; MountingHole_3.2mm_M3
J1: Conn_EXT; PinHeader_1x03_P2.54mm_Vertical
J2: Conn_HMI; PinHeader_1x05_P2.54mm_Vertical

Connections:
+3V3: J2.1; also elsewhere on the board
+24V: J1.1; also elsewhere on the board
GND: J1.2, J2.2; also elsewhere on the board
HMI_IRQ: J2.5; also elsewhere on the board
I2C_SCL: J2.4; also elsewhere on the board
I2C_SDA: J2.3; also elsewhere on the board
LINBUS: J1.3; also elsewhere on the board

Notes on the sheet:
Mechanics
+3V3 Board Supply
SAM-D21 Controller
Cortex Debug Interface
I2C Pull-up
LIN Driver
USB Communication
Audio Transducer
Terminals
+12V LIN Supply
Safety Pin
Power LED

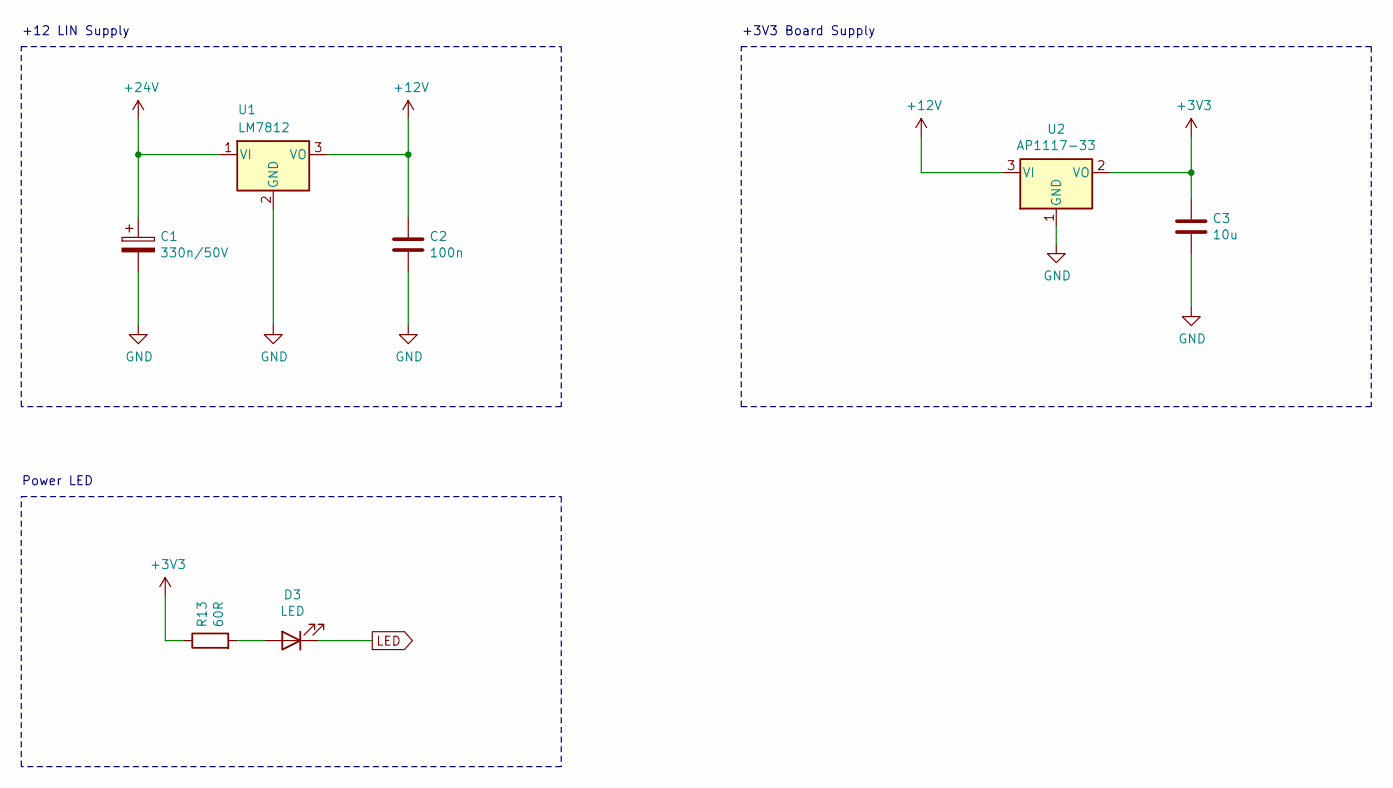
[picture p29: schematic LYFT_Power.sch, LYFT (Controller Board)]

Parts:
C1: 330n/50V; CP_Elec_4x5.4
C2: 100n; C_0805_2012Metric_Pad1.18x1.45mm_HandSolder
C3: 10u; C_0805_2012Metric_Pad1.18x1.45mm_HandSolder
D3: LED; LED_0805_2012Metric_Pad1.15x1.40mm_HandSolder
R13: 60R; R_0805_2012Metric_Pad1.20x1.40mm_HandSolder
U1: LM7812; TO-263-3_TabPin2
U2: AP1117-33; SOT-223-3_TabPin2

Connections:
+3V3: C3.1, R13.1, U2.2 (VO); also elsewhere on the board
+12V: C2.1, U1.3 (VO), U2.3 (VI); also elsewhere on the board
+24V: C1.1, U1.1 (VI); also elsewhere on the board
GND: C1.2, C2.2, C3.2, U1.2 (GND), U2.1 (GND); also elsewhere on the board
LED: D3.1 (K); also elsewhere on the board
unnamed: D3.2 (A), R13.2

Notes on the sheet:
+12 LIN Supply
+3V3 Board Supply
Power LED

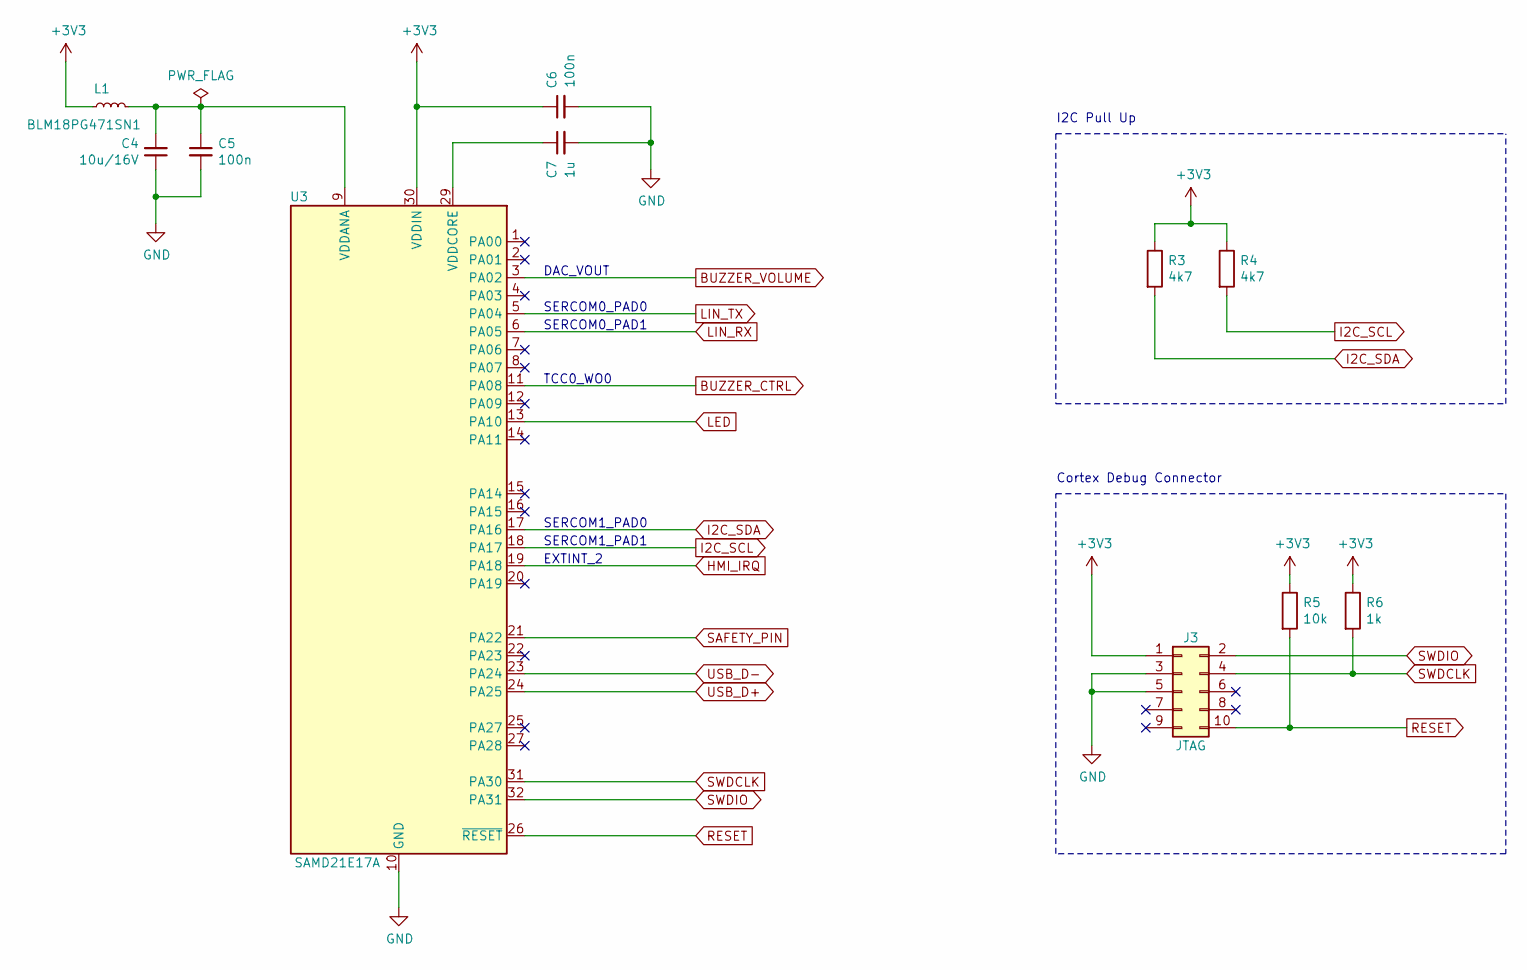
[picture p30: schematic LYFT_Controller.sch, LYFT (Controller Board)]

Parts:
C4: 10u/16V; C_0805_2012Metric_Pad1.18x1.45mm_HandSolder
C5, C6: 100n; C_0805_2012Metric_Pad1.18x1.45mm_HandSolder
C7: 1u; C_0805_2012Metric_Pad1.18x1.45mm_HandSolder
J3: JTAG; PinHeader_2x05_P1.27mm_Vertical
L1: BLM18PG471SN1; L_0805_2012Metric_Pad1.15x1.40mm_HandSolder
R3, R4: 4k7; R_0805_2012Metric_Pad1.20x1.40mm_HandSolder
R5: 10k; R_0805_2012Metric_Pad1.20x1.40mm_HandSolder
R6: 1k; R_0805_2012Metric_Pad1.20x1.40mm_HandSolder
U3: SAMD21E17A; TQFP-32_7x7mm_P0.8mm

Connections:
+3V3: C6.1, J3.1, L1.2, R3.1, R4.1, R5.1, R6.1, U3.30 (VDDIN); also elsewhere on the board
BUZZER_CTRL: U3.11 (PA08); also elsewhere on the board
BUZZER_VOLUME: U3.3 (PA02); also elsewhere on the board
GND: C4.1, C5.2, C6.2, C7.2, J3.3, J3.5, U3.10 (GND), U3.28 (GND); also elsewhere on the board
HMI_IRQ: U3.19 (PA18); also elsewhere on the board
I2C_SCL: R4.2, U3.18 (PA17); also elsewhere on the board
I2C_SDA: R3.2, U3.17 (PA16); also elsewhere on the board
LED: U3.13 (PA10); also elsewhere on the board
LIN_RX: U3.6 (PA05); also elsewhere on the board
LIN_TX: U3.5 (PA04); also elsewhere on the board
unnamed: C4.2, C5.1, L1.1, U3.9 (VDDANA)
unnamed: C7.1, U3.29 (VDDCORE)
RESET: J3.10, R5.2, U3.26 (~RESET)
SAFETY_PIN: U3.21 (PA22); also elsewhere on the board
SWDCLK: J3.4, R6.2, U3.31 (PA30)
SWDIO: J3.2, U3.32 (PA31)
USB_D+: U3.24 (PA25); also elsewhere on the board
USB_D-: U3.23 (PA24); also elsewhere on the board

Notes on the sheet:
Cortex Debug Connector
I2C Pull Up
TCC0_WO0
EXTINT_2
SERCOM0_PAD0
SERCOM0_PAD1
SERCOM1_PAD0
SERCOM1_PAD1
DAC_VOUT

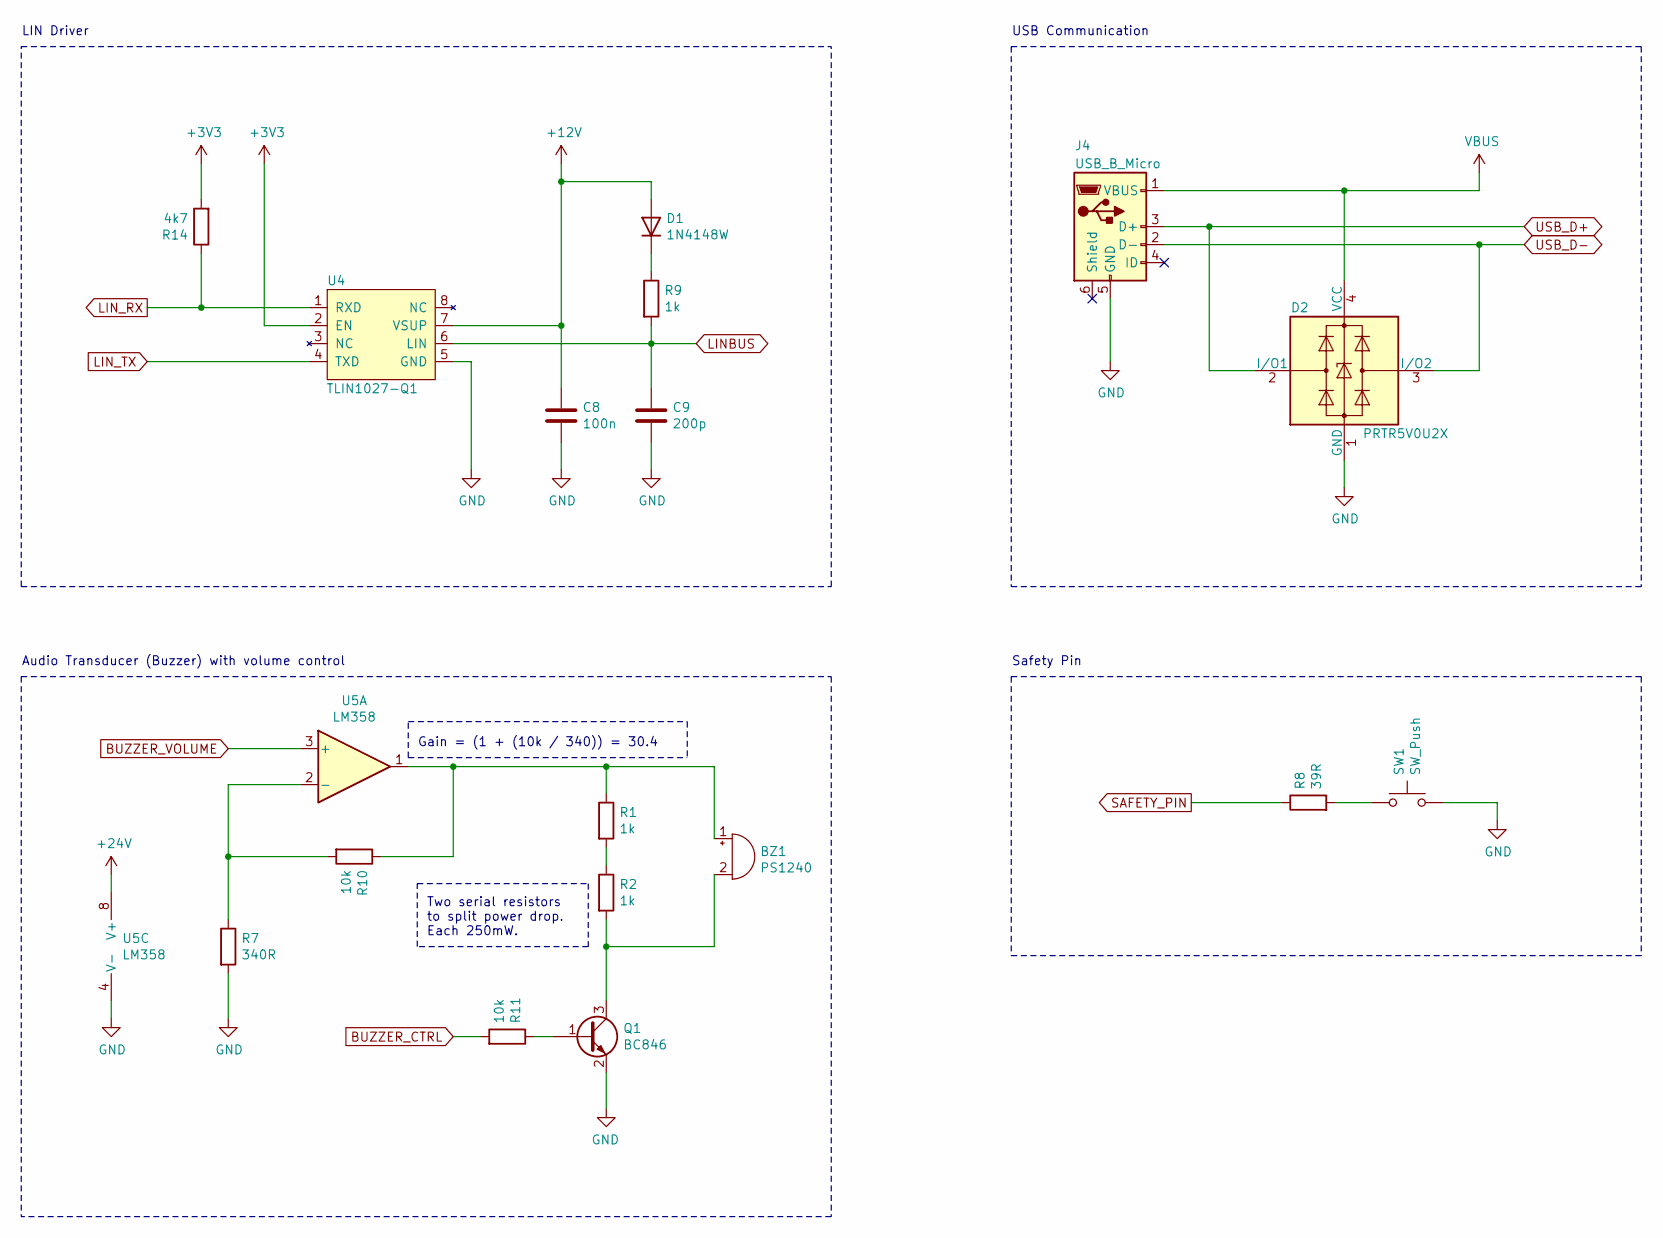
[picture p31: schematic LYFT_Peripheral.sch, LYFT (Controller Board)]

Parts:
BZ1: PS1240; Buzzer_TDK_PS1240P02BT_D12.2mm_H6.5mm
C8: 100n; C_0805_2012Metric_Pad1.18x1.45mm_HandSolder
C9: 200p; C_0805_2012Metric_Pad1.18x1.45mm_HandSolder
D1: 1N4148W; D_SOD-123
D2: PRTR5V0U2X; SOT-143
J4: USB_B_Micro; USB_Micro-B_Wuerth_614105150721_Vertical_CircularHoles
Q1: BC846; SOT-23
R1, R2, R9: 1k; R_0805_2012Metric_Pad1.20x1.40mm_HandSolder
R7: 340R; R_0805_2012Metric_Pad1.20x1.40mm_HandSolder
R8: 39R; R_0805_2012Metric_Pad1.20x1.40mm_HandSolder
R10, R11: 10k; R_0805_2012Metric_Pad1.20x1.40mm_HandSolder
R14: 4k7; R_0805_2012Metric_Pad1.20x1.40mm_HandSolder
SW1: SW_Push; SW_Tactile_SPST_Angled_PTS645Vx31-2LFS
U4: TLIN1027-Q1; SOIC-8_3.9x4.9mm_P1.27mm
U5: LM358; SO-8_3.9x4.9mm_P1.27mm

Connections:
+3V3: R14.2, U4.2 (EN); also elsewhere on the board
+12V: C8.2, D1.2 (A), U4.7 (VSUP); also elsewhere on the board
+24V: U5.8 (V+); also elsewhere on the board
BUZZER_CTRL: R11.2; also elsewhere on the board
BUZZER_VOLUME: U5.3 (+); also elsewhere on the board
GND: C8.1, C9.1, D2.1 (GND), J4.5 (GND), Q1.2 (E), R7.2, SW1.2, U4.5 (GND), U5.4 (V-); also elsewhere on the board
LINBUS: C9.2, R9.2, U4.6 (LIN); also elsewhere on the board
LIN_RX: R14.1, U4.1 (RXD); also elsewhere on the board
LIN_TX: U4.4 (TXD); also elsewhere on the board
unnamed: BZ1.1 (-), R1.1, R10.1, U5.1
unnamed: BZ1.2 (+), Q1.3 (C), R2.2
unnamed: D1.1 (K), R9.1
unnamed: Q1.1 (B), R11.1
unnamed: R1.2, R2.1
unnamed: R8.2, SW1.1
unnamed: R7.1, R10.2, U5.2 (-)
SAFETY_PIN: R8.1; also elsewhere on the board
USB_D+: D2.2 (I/O1), J4.3 (D+); also elsewhere on the board
USB_D-: D2.3 (I/O2), J4.2 (D-); also elsewhere on the board
VBUS: D2.4 (VCC), J4.1 (VBUS)

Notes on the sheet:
USB Communication
LIN Driver
Safety Pin
Audio Transducer (Buzzer) with volume control
Two serial resistors to split power drop. Each 250mW.
Gain = (1 + (10k / 340)) = 30.4

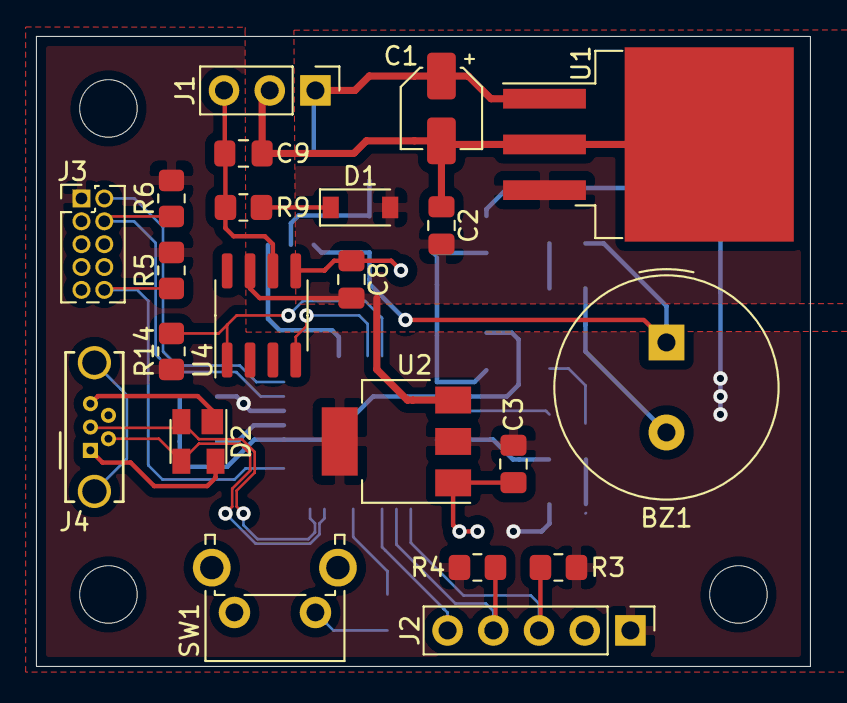
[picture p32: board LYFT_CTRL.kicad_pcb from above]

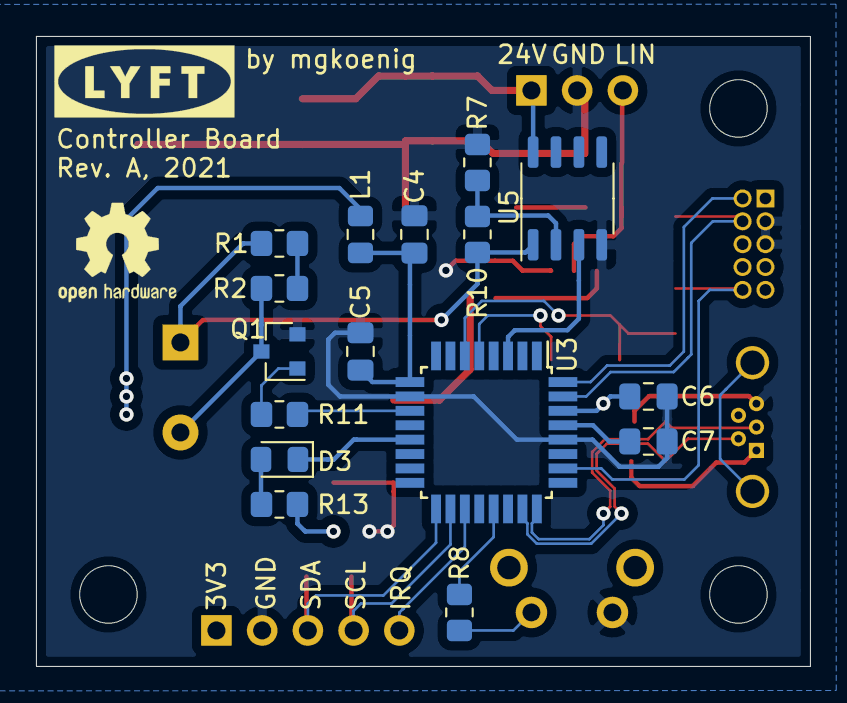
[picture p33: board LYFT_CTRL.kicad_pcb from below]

Board: 2 copper layers, 43.0 x 35.0 mm, 42 parts (17 on the bottom side), 30 nets.

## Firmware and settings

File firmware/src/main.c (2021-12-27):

/**
 * \file
 *
 * \brief Empty user application template
 *
 */

/**
 * \mainpage User Application template doxygen documentation
 *
 * \par Empty user application template
 *
 * Bare minimum empty user application template
 *
 * \par Content
 *
 * -# Include the ASF header files (through asf.h)
 * -# Minimal main function that starts with a call to system_init()
 * -# "Insert application code here" comment
 *
 */

/*
 * Include header files for all drivers that have been imported from
 * Atmel Software Framework (ASF).
 */
/*
 * Support and FAQ: visit <a href="https://www.microchip.com/support/">Microchip Support</a>
 */
#include <asf.h>
#include "lyft.h"

int main (void)
{
	system_init();
	lyft_init();

	while (1)
	{
		lyft_run();
	}
}

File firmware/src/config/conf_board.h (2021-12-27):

/**
 * \file
 *
 * \brief User board configuration template
 *
 * Copyright (c) 2013-2018 Microchip Technology Inc. and its subsidiaries.
 *
 * \asf_license_start
 *
 * \page License
 *
 * Subject to your compliance with these terms, you may use Microchip
 * software and any derivatives exclusively with Microchip products.
 * It is your responsibility to comply with third party license terms applicable
 * to your use of third party software (including open source software) that
 * may accompany Microchip software.
 *
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
 * \asf_license_stop
 *
 */
/*
 * Support and FAQ: visit <a href="https://www.microchip.com/support/">Microchip Support</a>
 */

#ifndef CONF_BOARD_H
#define CONF_BOARD_H


/************************************************************************/
/* I2C MODULE                                                           */
/************************************************************************/
#define I2C_MODULE							SERCOM1
#define I2C_PINMUX_PAD0						PINMUX_PA16C_SERCOM1_PAD0
#define I2C_PINMUX_PAD1						PINMUX_PA17C_SERCOM1_PAD1

/************************************************************************/
/* LIN MODULE                                                           */
/************************************************************************/
#define LIN_MODULE							SERCOM0
#define LIN_MUXSET							USART_RX_1_TX_0_XCK_1
#define LIN_PINMUX_PAD0						PINMUX_PA04D_SERCOM0_PAD0
#define LIN_PINMUX_PAD1						PINMUX_PA05D_SERCOM0_PAD1
#define LIN_PIN_TX							PIN_PA04
#define LIN_PIN_RX							PIN_PA05

/************************************************************************/
/* EXTERNAL INTERRUPT PIN SETTINGS                                      */
/************************************************************************/
#define IRQ_PIN_KEYPAD						PIN_PA18A_EIC_EXTINT2
#define IRQ_MUX_KEYPAD						PINMUX_PA18A_EIC_EXTINT2
#define IRQ_EIC_KEYPAD						2		// Ext. Int. Controller Line

/************************************************************************/
/* AUDIO CONTROL                                                        */
/************************************************************************/
#define AUDIO_WAVE_GENERATOR_PIN			PIN_PA08E_TCC0_WO0
#define AUDIO_WAVE_GENERATOR_PINMUX			PINMUX_PA08E_TCC0_WO0

/************************************************************************/
/* GPIO PINS                                                            */
/************************************************************************/
#define GPIO_PIN_LED						PIN_PA10
#define GPIO_PIN_SAFETY						PIN_PA22


#endif // CONF_BOARD_H

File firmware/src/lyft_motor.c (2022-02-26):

/*
 * lyft_motor.c
 *
 * Created: 19/11/2021 14:01:37
 *  Author: Matthias Koenig
 */ 

#include "lyft_motor.h"


uint16_t			mot_pos_a;
uint16_t			mot_pos_b;
uint16_t			mot_pos_hi;
uint16_t			mot_pos_lo;
uint8_t				mot_state_a;
uint8_t				mot_state_b;
uint8_t				prev_cmd;
uint8_t				braking_distance;
uint8_t				safety_procedure;
uint8_t				safety_command;
enum motor_mode		op_mode;


static void			motor_burst(void);
static void			motor_startup(void);
static void			motor_sendStartupPacket(uint8_t byte0, uint8_t byte1, uint8_t byte2, uint8_t byte3);
static uint8_t		motor_readStartupPacket(void);
static void			motor_sendCommand(uint16_t pos, uint8_t cmd);

static void			motor_move_up(void);
static void			motor_move_down(void);
static void			motor_move_stop(void);
static void			motor_calibrate(void);
static void			motor_safety_protocol(void);


const uint8_t	zero_packet[3] = {0, 0, 0};	
const uint8_t   sfin_packet[3] = {246, 255, 191};		// startup finishing packet
const uint8_t	startup_sequence[STARTUP_SEQUENCE_LENGTH][(STARTUP_PACKET_LENGTH/2)] = {
	{255,   7, 255, 255},       // seq_idx 0 (no resp)
	{255,   7, 255, 255},       // seq_idx 1 (no resp)
	{255,   1,   7, 255},       // seq_idx 2 (no resp)
	{208,   2,   7, 255},       // seq_idx 3
	{0,     2,   7, 255},       // seq_idx 4 LOOP_A until resp > 0
	{0,     6,   9,   0},       // seq_idx 5
	{0,     6,  12,   0},       // seq_idx 6
	{0,     6,  13,   0},       // seq_idx 7
	{0,     6,  10,   0},       // seq_idx 8
	{0,     6,  11,   0},       // seq_idx 9
	{0,     4,   0,   0},       // seq_idx 10
	{0,     2,   0,   0},       // seq_idx 11 LOOP_B until resp > 0
	{0,     6,   9,   0},       // seq_idx 12
	{0,     6,  12,   0},       // seq_idx 13
	{0,     6,  13,   0},       // seq_idx 14
	{0,     6,  10,   0},       // seq_idx 15
	{0,     6,  11,   0},       // seq_idx 16
	{0,     4,   1,   0},       // seq_idx 17
	{0,     2,   1,   0},       // seq_idx 18 LOOP_C while seq < 8 (no resp)
	{208,   1,   7,   0},       // seq_idx 19 (no resp)
	{208,   2,   7,   0}        // seq_idx 20 (no resp)
};


void motor_init(void)
{
	hal_lin_init();
	hal_delay_msec(250);
	motor_startup();
	
	safety_command = MOTOR_CMD_IDLE;
	safety_procedure = MOTOR_SAFETY_PROTOCOL;
	//op_mode = MOTOR_MODE_NORMAL;
	op_mode = MOTOR_MODE_READY;
}

enum motor_mode motor_run(enum motor_event mot_ev)
{	
	motor_burst();
	
	if ((mot_state_a == MOTOR_STATE_BLOCKAGE) || (mot_state_b == MOTOR_STATE_BLOCKAGE))
	{
		if (safety_procedure == MOTOR_SAFETY_PROTOCOL)
		{
			op_mode = MOTOR_MODE_CRITICAL;
			safety_procedure = 0;
			
			if (prev_cmd == MOTOR_CMD_MOVE_UP) {
				safety_command = MOTOR_CMD_MOVE_DOWN;
			} else if (prev_cmd == MOTOR_CMD_MOVE_DOWN) {
				safety_command = MOTOR_CMD_MOVE_UP;
			} else {
				safety_command = MOTOR_CMD_MOVE_STOP;
			}
		}	
	}
	
	if (op_mode == MOTOR_MODE_CRITICAL)
	{
		motor_safety_protocol();
	}
	else if (op_mode == MOTOR_MODE_CALIBRATION) {
		motor_calibrate();
	}
	else 
	{
		switch (mot_ev)
		{
			case MOTOR_EVENT_MOVE_UP: motor_move_up(); op_mode = MOTOR_MODE_MOVE; break;
			case MOTOR_EVENT_MOVE_DOWN: motor_move_down(); op_mode = MOTOR_MODE_MOVE; break;
			case MOTOR_EVENT_STOP: motor_move_stop(); op_mode = MOTOR_MODE_READY; break;
			case MOTOR_EVENT_CALIBRATE: op_mode = MOTOR_MODE_CALIBRATION; break;
			default: motor_move_stop; op_mode = MOTOR_MODE_READY; break;
		}		
	}	
	
	return op_mode;
}

uint8_t motor_getDrift(void)
{
	return (uint8_t) (mot_pos_hi - mot_pos_lo);
}

uint16_t motor_getPosition(void)
{
	return ((mot_pos_a + mot_pos_b) / 2);
}

uint16_t motor_getHeightInch(uint8_t offset)
{
	uint16_t pos, height;
	
	pos = ((mot_pos_a + mot_pos_b) / 2);
	height = ((pos / MOTOR_STEP_SIZE) + MOTOR_BASE);
	height = (height + offset - MOTOR_OFFSET_RANGE);
	height = ((height / 2.54) * 10);
	
	return height;
}

uint16_t motor_getHeightCentimeter(uint8_t offset)
{
	uint16_t pos, height;
	
	pos = ((mot_pos_a + mot_pos_b) / 2);
	height = ((pos / MOTOR_STEP_SIZE) + MOTOR_BASE);
	height = (height + offset - MOTOR_OFFSET_RANGE);
	
	return height;
}


static void motor_burst(void)
{
	uint8_t			i;
	static uint8_t	rx_data[MOTOR_PACKET_LEN_RX];
	
	hal_lin_write(NODE_SEVENTEEN, zero_packet, ZERO_PACKET_LEN);
	hal_delay_msec(MOTOR_DELAY_RX);
		
	hal_lin_read(NODE_MOTOR_A, rx_data, MOTOR_PACKET_LEN_RX);
	mot_pos_a = ((rx_data[3] << 8) | ( rx_data[2]));
	mot_state_a = rx_data[4];
	hal_delay_msec(MOTOR_DELAY_RX);
		
	hal_lin_read(NODE_MOTOR_B, rx_data, MOTOR_PACKET_LEN_RX);
	mot_pos_b = ((rx_data[3] << 8) | ( rx_data[2]));
	mot_state_b = rx_data[4];
	hal_delay_msec(MOTOR_DELAY_RX);
		
	for (i=0; i<6; i++)
	{
		hal_lin_read(NODE_SIXTEEN, NULL, 0);
		hal_delay_msec(MOTOR_DELAY_RX);
	}
		
	hal_lin_read(NODE_ONE, NULL, 0);
	hal_delay_msec(MOTOR_DELAY_RX);
	
	if (mot_pos_a != mot_pos_b) {
		mot_pos_lo = MIN(mot_pos_a, mot_pos_b);
		mot_pos_hi = MAX(mot_pos_a, mot_pos_b);
	} else {
		mot_pos_hi = mot_pos_a;
		mot_pos_lo = mot_pos_a;
	}
}

static void motor_move_up(void)
{
	uint8_t			cmd = MOTOR_CMD_MOVE_STOP;
	uint16_t		pos = mot_pos_a;
	
	if (mot_pos_hi < MOTOR_POSITION_MAX)
	{		
		if ((mot_state_a == MOTOR_STATE_IDLE) && (mot_state_b == MOTOR_STATE_IDLE))
		{
			if (prev_cmd == MOTOR_CMD_IDLE) 
			{
				pos = mot_pos_a;
				cmd = MOTOR_CMD_MOVE_START;
			}
			else if (prev_cmd == MOTOR_CMD_MOVE_START)
			{
				pos = mot_pos_lo;
				cmd = MOTOR_CMD_MOVE_UP;
			}
		}
		else if ((mot_state_a == MOTOR_STATE_MOVING) && (mot_state_b == MOTOR_STATE_MOVING))
		{
			if (prev_cmd == MOTOR_CMD_MOVE_UP)
			{
				pos = mot_pos_lo;
				cmd = MOTOR_CMD_MOVE_UP;
			}
		}
		
		braking_distance = 0;
		motor_sendCommand(pos, cmd);
	}
	else 
	{
		motor_move_stop();
	}
}

static void motor_move_down(void)
{
	uint8_t			cmd = MOTOR_CMD_MOVE_STOP;
	uint16_t		pos = mot_pos_a;
	
	if (mot_pos_lo > MOTOR_POSITION_MIN)
	{
		if ((mot_state_a == MOTOR_STATE_IDLE) && (mot_state_b == MOTOR_STATE_IDLE))
		{
			if (prev_cmd == MOTOR_CMD_IDLE)
			{
				pos = mot_pos_a;
				cmd = MOTOR_CMD_MOVE_START;
			}
			else if (prev_cmd == MOTOR_CMD_MOVE_START)
			{
				pos = mot_pos_hi;
				cmd = MOTOR_CMD_MOVE_DOWN;
			}
		}
		else if ((mot_state_a == MOTOR_STATE_MOVING) && (mot_state_b == MOTOR_STATE_MOVING))
		{
			if (prev_cmd == MOTOR_CMD_MOVE_DOWN)
			{
				pos = mot_pos_hi;
				cmd = MOTOR_CMD_MOVE_DOWN;
			}
		}
		
		braking_distance = 0;
		motor_sendCommand(pos, cmd);
	}
	else
	{
		motor_move_stop();
	}
}
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

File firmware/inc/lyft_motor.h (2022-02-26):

/**
 * @file lyft_motor.h
 * @author Matthias Koenig (mgkoenig) 
 * @date 19 Nov 2021 
 * @brief LYFT Motor Driver
 *
 * @details The motor driver contains all node IDs which are used 
 * on the LIN bus as well as all commands and states of the motor 
 * control. 
 *
 * Some naming convention:
 * - Step value: the motors specify their current position with 
 * numerical values between 162 and 6537. These values do not represent
 * a certain height in centimeters rather than a stepper position. 
 * - Position: the desk position equals the numerical value of the 
 * the stepper motors. It's the current height of the desk represented 
 * as 'step value'. 
 * - Height: the desk height is the current height of the desk represented 
 * as inch or centimeter value. This value gives the user a concrete 
 * idea of the desk's position. The desk height is directly connected to 
 * the desk position. 
 */

#ifndef LYFT_MOTOR_H_
#define LYFT_MOTOR_H_


#include <asf.h>
#include "hal_lin.h"
#include "hal_delay.h"
#include "lyft_util.h"


#define NODE_ONE							1			/**< LIN node ID 1 */
#define NODE_MOTOR_A						8			/**< LIN node ID 8 (Motor A) */
#define NODE_MOTOR_B						9			/**< LIN node ID 9 (Motor B) */
#define NODE_SIXTEEN						16			/**< LIN node ID 16 */
#define NODE_SEVENTEEN						17			/**< LIN node ID 17 */
#define NODE_MASTER							18			/**< LIN node ID 18 (Master) */

#define STARTUP_PACKET_LENGTH				8			/**< Each data packet of the startup sequence has a length of 8 bytes */
#define STARTUP_SEQUENCE_LENGTH				21			/**< The startup sequence consists of 21 data packets */

#define STARTUP_SEQUENCE_LOOP_IDX_A			4			/**< The startup packet #4 will be re-transmitted */
#define STARTUP_SEQUENCE_LOOP_IDX_B			11			/**< The startup packet #11 will be re-transmitted */
#define STARTUP_SEQUENCE_LOOP_IDX_C			18			/**< The startup packet #18 will be re-transmitted */
#define STARTUP_SEQUENCE_ITERATION			8			/**< The looped packets will be re-transmitted 8 times */

#define MOTOR_DELAY_TX						12			/**< When a packet was sent wait for 12ms before writing new data */
#define MOTOR_DELAY_RX						5			/**< When a packet was received wait for 5ms before receiving new data */

#define MOTOR_PACKET_LEN_RX					6			/**< A data packet received from a motor is always 6 bytes in length */
#define MOTOR_PACKET_LEN_CMD				3			/**< A motor command packet contains always 3 bytes of data (2 bytes position, 1 byte command) */
#define ZERO_PACKET_LEN						3			/**< A zero packet consists of three zero bytes (0x00, 0x00, 0x00)  */
#define FINISH_PACKET_LEN					3			/**< The data packet to finalize the startup sequence consists of three bytes */

#define MOTOR_CMD_IDLE						0xFC		/**< Motor command idle */
#define MOTOR_CMD_MOVE_START				0xC4		/**< Motor command to announce a moving command */
#define MOTOR_CMD_MOVE_UP					0x86		/**< Motor command move up */
#define MOTOR_CMD_MOVE_DOWN					0x85		/**< Motor command move down */
#define MOTOR_CMD_MOVE_SLOW					0x87		/**< Motor command move slow */
#define MOTOR_CMD_MOVE_STOP					0x84		/**< Motor command stop */
#define MOTOR_CMD_LIMIT_START				0x80		/**< Motor command when trying to go above/beneath the limit */
#define MOTOR_CMD_LIMIT_HIGH				0x82		/**< Motor command when upper limit is reached */
#define MOTOR_CMD_LIMIT_LOW					0x81		/**< Motor command when lower limit is reached */

#define MOTOR_CMD_CALIBRATION_START			0xC4		/**< Motor command to announce a calibration */
#define MOTOR_CMD_CALIBRATION				0xBD		/**< Motor command calibrate */
#define MOTOR_CMD_CALIBRATION_STOP			0xBC		/**< Motor command to finish calibration */

#define MOTOR_STATE_IDLE					0x00		/**< Motor state idle */
#define MOTOR_STATE_CALIBRATED				0x01		/**< Motor state calibrated (finished) */
#define MOTOR_STATE_MOVING					0x02		/**< Motor state moving */
#define MOTOR_STATE_MOVING_SLOW				0x03		/**< Motor state moving slow */
#define MOTOR_STATE_CALIBRATING				0x04		/**< Motor state calibrating (ongoing) */
#define MOTOR_STATE_LIMIT_A					0xA5		/**< Motor state unknown (measured on LIN bus) */
#define MOTOR_STATE_LIMIT_B					0x25		/**< Motor state unknown (measured on LIN bus) */
#define MOTOR_STATE_BLOCKAGE				0x62		/**< Motor state blocked (error state) */
#define MOTOR_STATE_ERROR					0x65		/**< Motor state general error condition */

#define MOTOR_SAFETY_PROTOCOL				23			/**< The safety protocol consists of 23 steps */
#define MOTOR_SAFETY_MARGIN					100			/**< No motor movement if position difference is less than 100 'step values' */
#define MOTOR_POSITION_MIN					200			/**< Lowest desk position (about 62cm) */
#define MOTOR_POSITION_MAX					6400		/**< Highest desk position (about 124cm) */

#define MOTOR_SERVICE_INTERVAL				50			/**< Run motor burst every 50ms */
#define MOTOR_BRAKING_DISTANCE				5			/**< Before stopping the motors move slow for 5 iterations (measured from original controller) */

#define MOTOR_STEP_SIZE						100			/**< 100 motor steps per centimeter */
#define MOTOR_BASE							60			/**< Lowest desk position in centimeter */

#define MOTOR_OFFSET_RANGE					9			/**< Fine adjust of desk height by plus/minus 9cm for the displayed value */


/** 
 * @enum motor_mode 
 * The motors might be busy in different operation modes. 
 */
enum motor_mode {
	//MOTOR_MODE_NORMAL,			/**< Motors are ready and operating normal */
	MOTOR_MODE_READY,
	MOTOR_MODE_MOVE,
	MOTOR_MODE_CALIBRATION,		/**< Motors are currently calibrating */
	MOTOR_MODE_CRITICAL			/**< Motors got stuck and are therefore in a critical condition */
};

/** 
 * @enum motor_event 
 * The motors might be triggered for some action with different events. 
 */
enum motor_event {
	//MOTOR_EVENT_IDLE,
	MOTOR_EVENT_STOP,			/**< Stop moving motors */
	MOTOR_EVENT_MOVE_UP,		/**< Move motors up */
	MOTOR_EVENT_MOVE_DOWN,		/**< Move motors down */
	MOTOR_EVENT_CALIBRATE		/**< Calibrate both motors (to reduce drift) */
};


/** 
 * @brief Motor initialization 
 *
 * Initializes the LIN module and run the startup procedure
 * to get both motors ready. 
 */
void motor_init(void);

/** 
 * @brief Periodic motor service routine
 *
 * This routine is called periodically to retrieve motor states, positions and 
 * to trigger motor actions like moving or stopping. 
 *
 * @param[in] mot_ev An event to be triggered like #MOTOR_EVENT_MOVE_UP
 *
 * @return Returns the current motor mode like #MOTOR_MODE_NORMAL, #MOTOR_MODE_CALIBRATION or #MOTOR_MODE_CRITICAL
 */
enum motor_mode motor_run(enum motor_event mot_ev);

/** 
 * @brief Get the motor drift 
 *
 * This functions returns the absolute drift of both motor positions to 
 * each other. The smaller the value the better. 
 *
 * @return The absolute drift value as 'step value'
 */
uint8_t motor_getDrift(void);
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

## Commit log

2021-12-27 Updated latest schematic file
2022-02-12 v1.0.1
    Improved behaviour if no safety pin is plugged-in while display is on.
2022-02-13 added "button map"
2022-02-22 added documentation
    Removed #defines of current SW version since they are nowhere used.
2022-02-26 [feature] automatic drive mode
    - New feature: automatic drive mode
    - Code improvements: utility function to compute difference as absolute value, screen behaviour on start-up without safety pin)
    - Code optimizations (unified button actions to common functions)
    - Adjusted motor controls (min/max values and safety margin)
    - Further documentations
